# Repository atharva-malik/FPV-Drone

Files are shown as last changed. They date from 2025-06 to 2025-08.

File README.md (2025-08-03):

# Ghast Drone
While playing Minecraft, I entered the Ghast while in spectator mode, and wondered what it would be like to fly in it IRL. Therefore I designed the following project.
<p align="center">
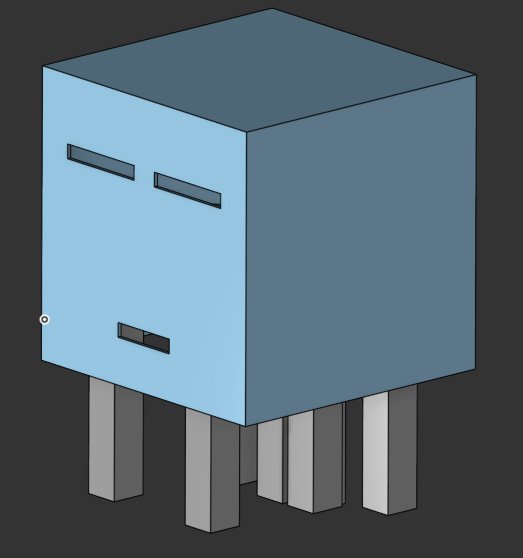
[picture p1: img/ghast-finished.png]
  
</p>
I have attached the picture of the look that I am going for. I will replace this with the finished build once it is done.

# BOM
The BOM is available in the [BOM.csv](BOM.csv) file. It contains all the parts required to build the drone, along with links to where they can be purchased. On a glance:
| Part Name | Source | Price |
|---|---|---|
|HappyModel EP1 EP2 RX 2.4G ExpressLRS| https://www.aliexpress.com/item/1005008247370304.html | $21.35|
|Custom Frame| \3D Models\Frame Base.stl | $30|
|iFlight XING-E Pro 2207 1800KV| https://www.aliexpress.com/item/1005007751252503.html | $85.66|
|Gemfan Hurricane 51477 3-Blade| https://www.aliexpress.com/item/1005008235140623.html | $4.29|
|SpeedyBee F405 Stack| https://www.aliexpress.com/item/1005005646570050.html | $136.07|
|Caddx Ratel 2 V2| https://www.aliexpress.com/item/1005006156850612.html | $30.67|
|XILO STAX 5.8GHz FPV Video Transmitter (25-600mW) w/ Smart Audio| https://www.getfpv.com/xilo-stax-5-8ghz-fpv-video-transmitter-25-600mw.html | $38.99|
|6S 1480mAh 150C Battery| https://www.aliexpress.com/item/1005007537503660.html | $73.84|
|Lipo Charger| https://uk.banggood.com/IMAX-B6-80W-6A-Lipo-Battery-Balance-Charger-T-Plug-with-Power-Supply-Adapter-p-1401686.html | $39.75|
|Heat Shrink| https://www.aliexpress.com/item/1005005088669576.html | $11.51|
|DVR| https://au.banggood.com/Eachine-ProDVR-Pro-DVR-Video-Audio-Mini-Recorder-for-FPV-Multicopters-for-RC-Drone-FPV-Racing-p-1061196.html | $16.11|
|GRAND TOTAL (AUD) | | $488.24|
|GRAND TOTAL (USD) | | $316.58|

The total cost currently comes out to ~$300 USD, bear in mind that this is without the cost of the 3D printed parts or the shipping costs. The cost of the drone parts will vary depending on where you live and where you buy the parts from.

# Firmware
For the firmware, I will be using the tried and tested [BetaFlight](https://betaflight.com/) firmware. This firmware is widely used in the FPV community and has a lot of features that will be useful for my drone. I should be able to customise it to give it the "floaty" feel of the Ghast.

# Wiring Instructions
All of the parts need to be wired according to the following schematic:
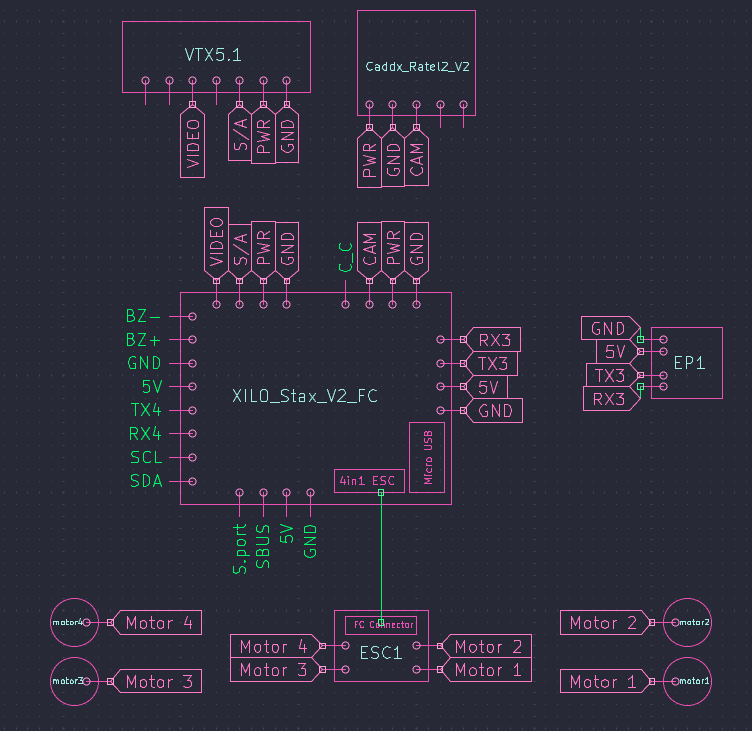
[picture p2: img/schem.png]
Schematic


# 3D Printed Parts
The 3D printed parts are all under the 3D Models folder in the repository. It contains the STL files for a carrying case, a GoPro mount, and the Ghast body and tentacles. The 3D printed parts are all designed to be printed with standard PLA filament.

# 3D Model
Drone

The 3D model of the Ghast is available in the [3D Models](/3D%20Models/Proof%20of%20Concept/).

# Frame Design
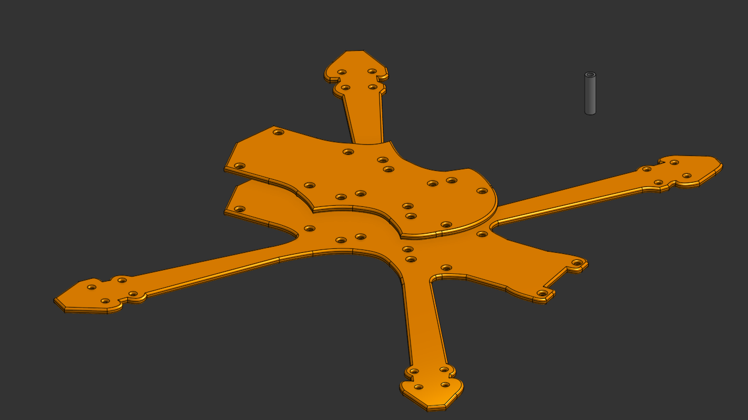
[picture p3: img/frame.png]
Frame


# Credits
I would like to thank @Mikuel for [this](https://www.aos-rc.com/aos-labs) link which explained drone motors to me.

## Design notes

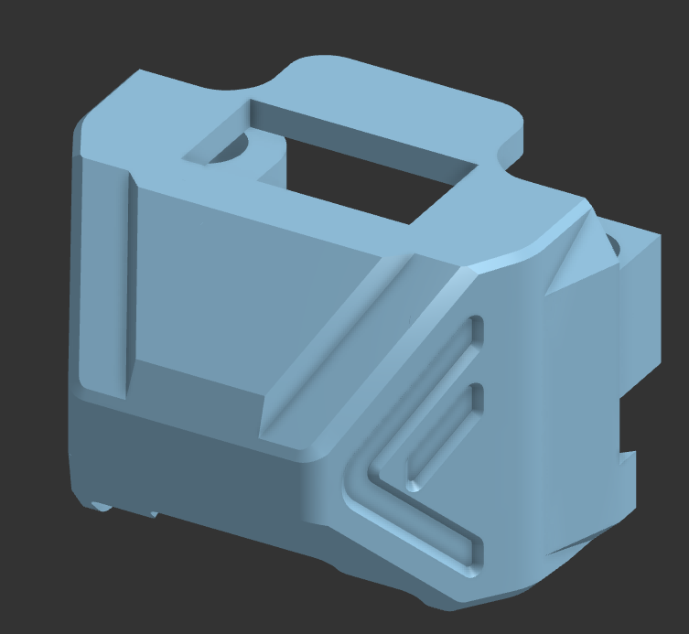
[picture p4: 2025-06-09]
img/POC/Backplate (XT60 Connector).png

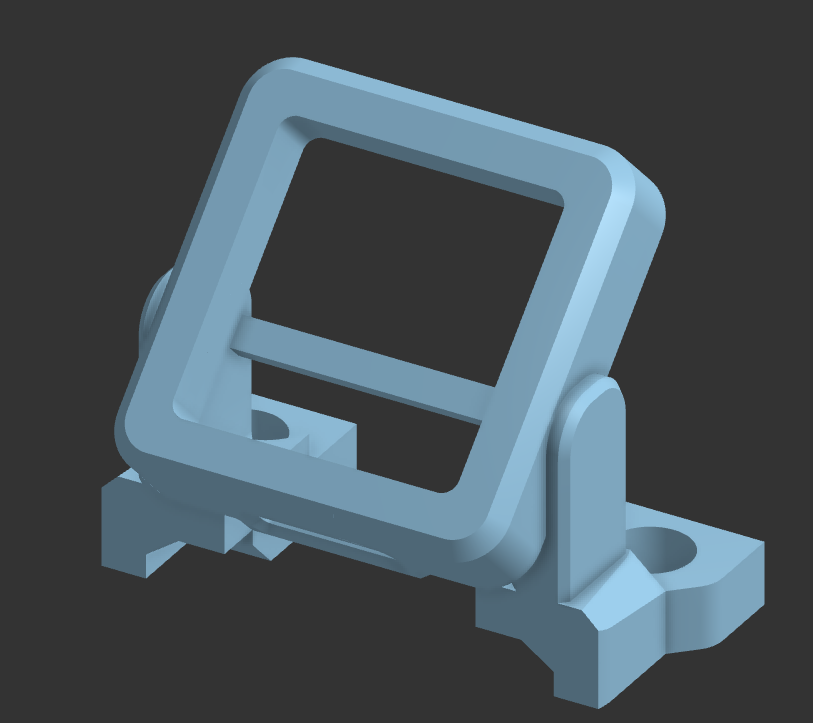
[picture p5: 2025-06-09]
img/POC/GPS Mount High.png

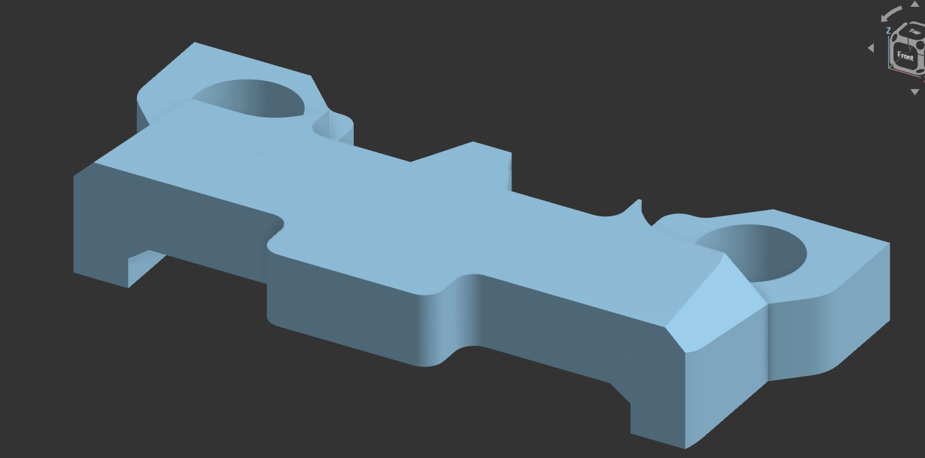
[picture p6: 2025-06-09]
img/POC/GPS - Flat Mount.png

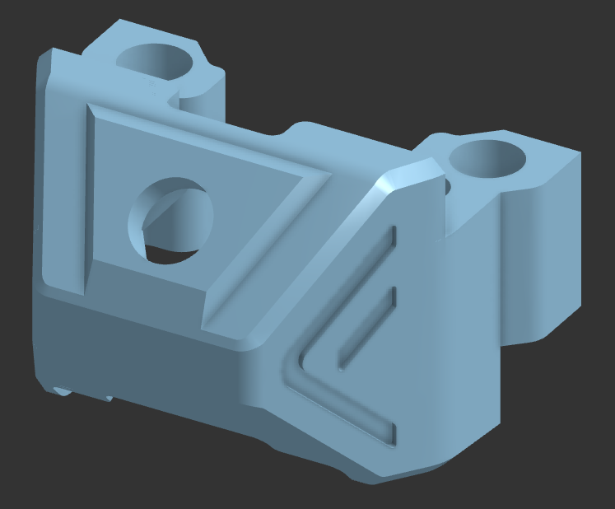
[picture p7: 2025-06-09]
img/POC/Analog Transmitter Mount.png

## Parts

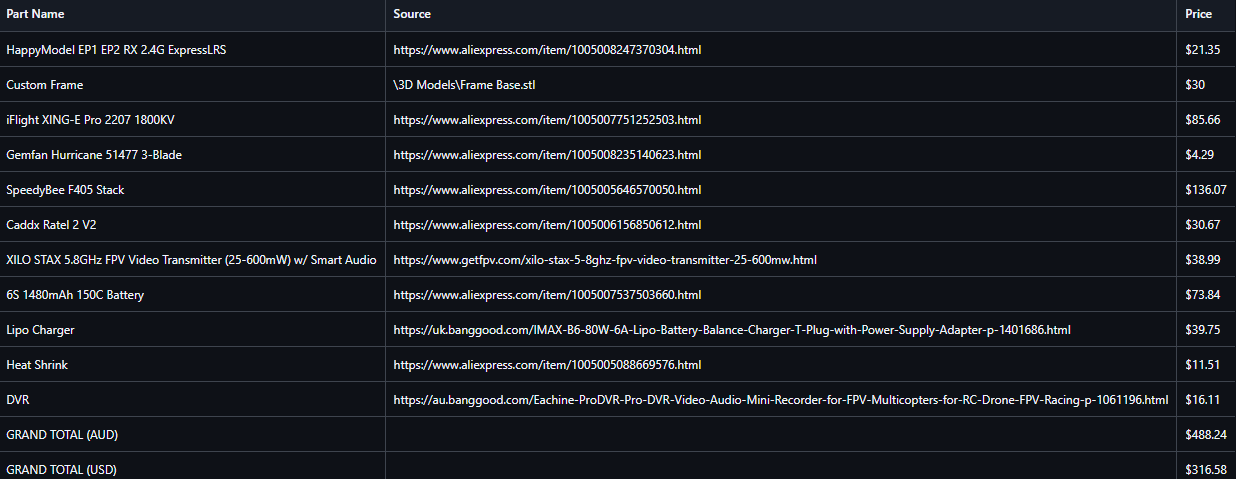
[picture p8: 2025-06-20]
img/BOM.png

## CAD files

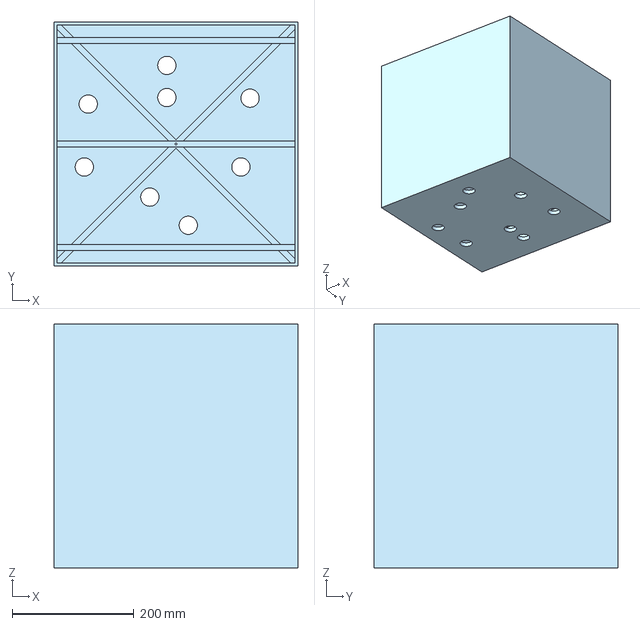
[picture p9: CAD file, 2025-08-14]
3D Models/Ghast Body.step
400.0 x 400.0 x 400.0 mm

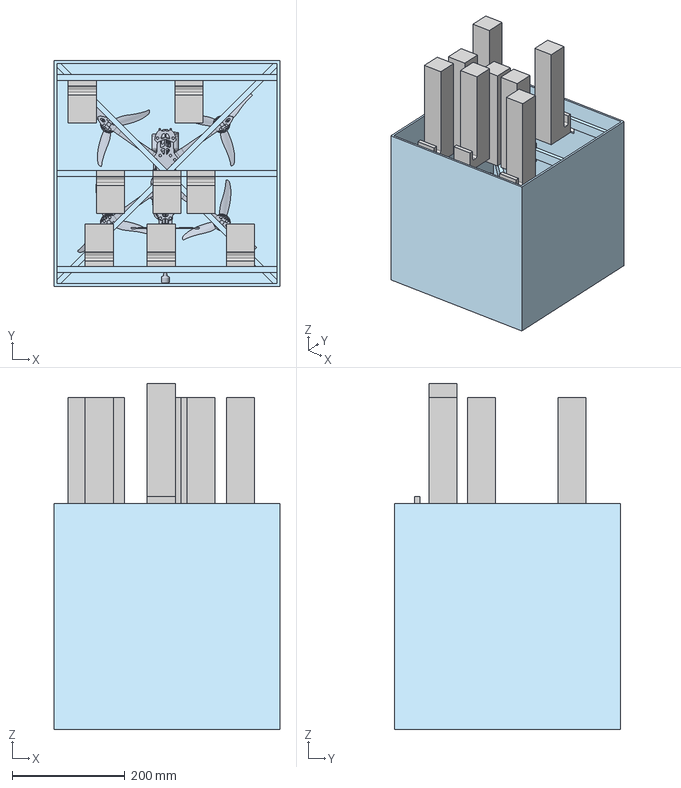
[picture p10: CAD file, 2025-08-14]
3D Models/Proof of Concept/Ghast - Clean.step
400.0 x 400.0 x 612.5 mm
Tentacle x 8
Ghast Body
id24
id29
id34
id39
id44
id49
id54
id59
id64
id69
id74
id79
id84
id89
id94
id99
id104
id109
id114
id119
id124
id129
id134
id139
id144
id149
id154
id159
id164
id169
id174
id179
id184
id189
id194
id199
id204
id209
id214
id219
id224
id229
id234
id239
id244
id249
id254
id259
id264
id269
id274
id279
id284
id289
id294
id299
id304
id309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

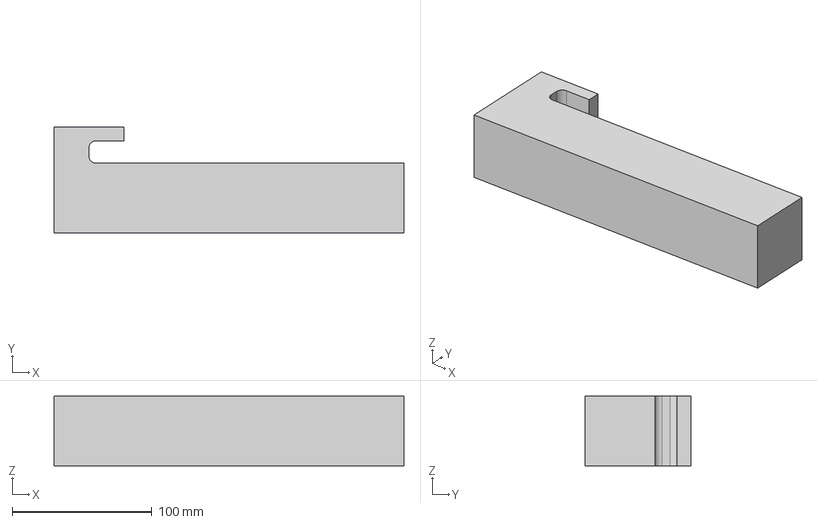
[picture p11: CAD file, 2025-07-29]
3D Models/Tentacle.step
250.0 x 76.0 x 50.0 mm

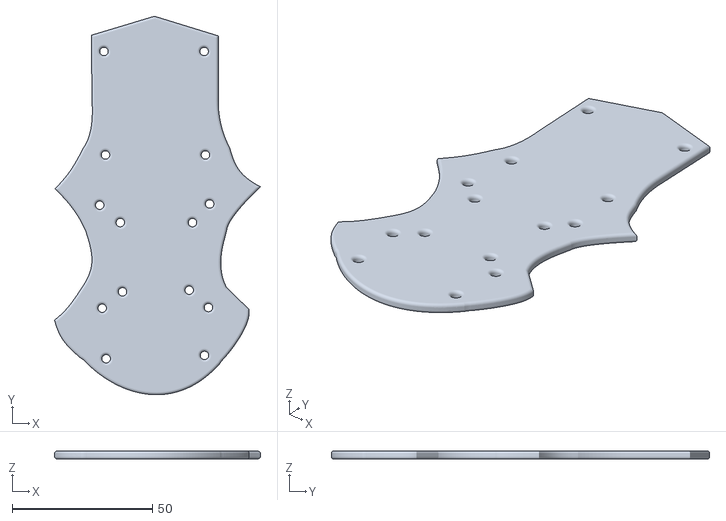
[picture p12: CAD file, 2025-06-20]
3D Models/Frame Top.stl
73.5 x 135.0 x 3.00

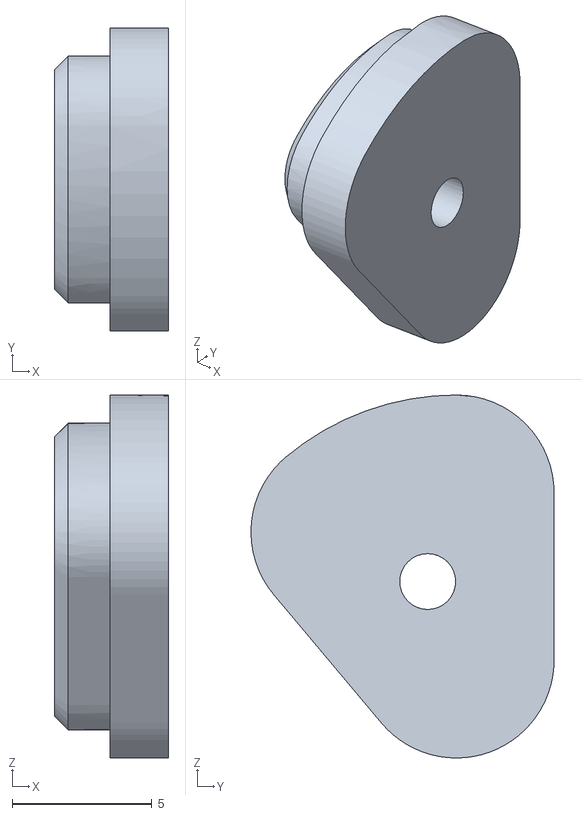
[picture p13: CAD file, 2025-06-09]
3D Models/Proof of Concept/Camera Mount (Analog).stl
4.10 x 10.9 x 13.0

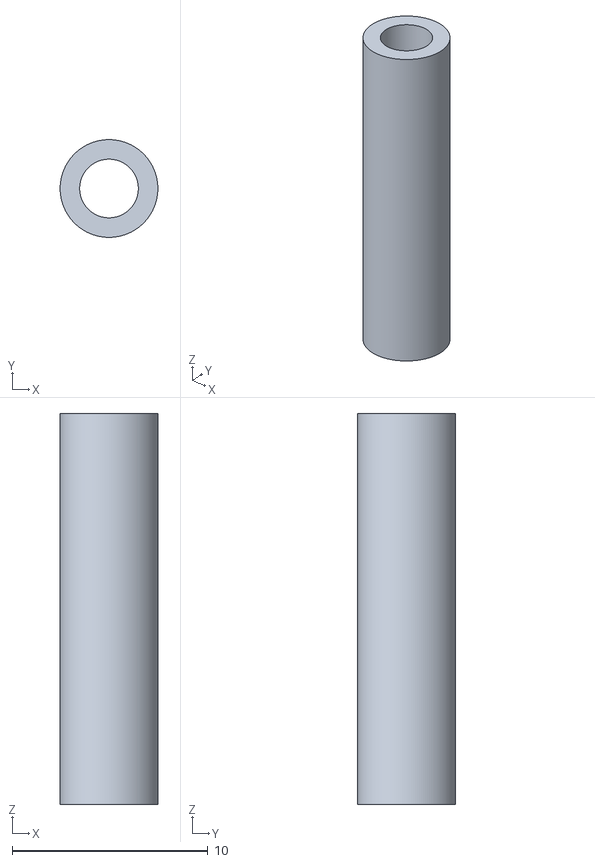
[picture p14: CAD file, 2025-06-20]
3D Models/Standoff.stl
5.00 x 5.00 x 20.0

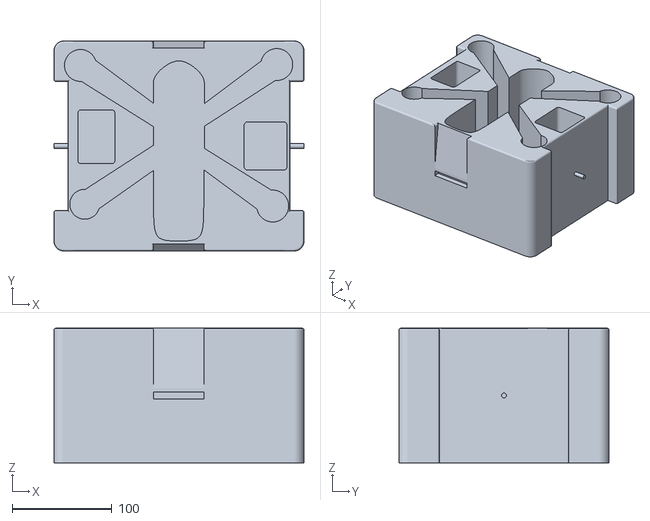
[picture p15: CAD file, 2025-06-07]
3D Models/Case Bottom.stl
250.8 x 210.8 x 135.0

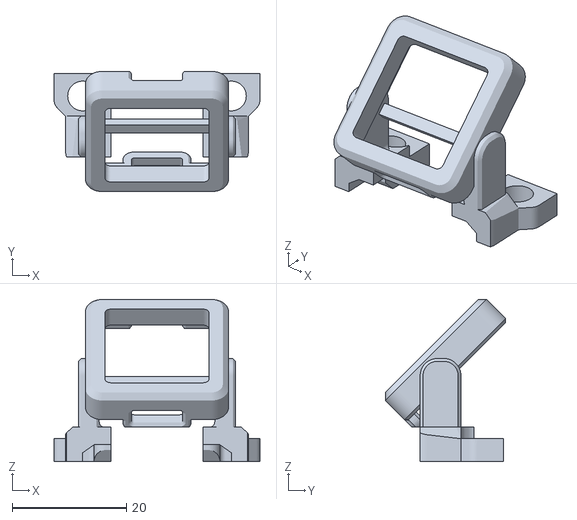
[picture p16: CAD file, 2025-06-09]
3D Models/Proof of Concept/GPS Mount High.stl
36.0 x 21.0 x 28.3

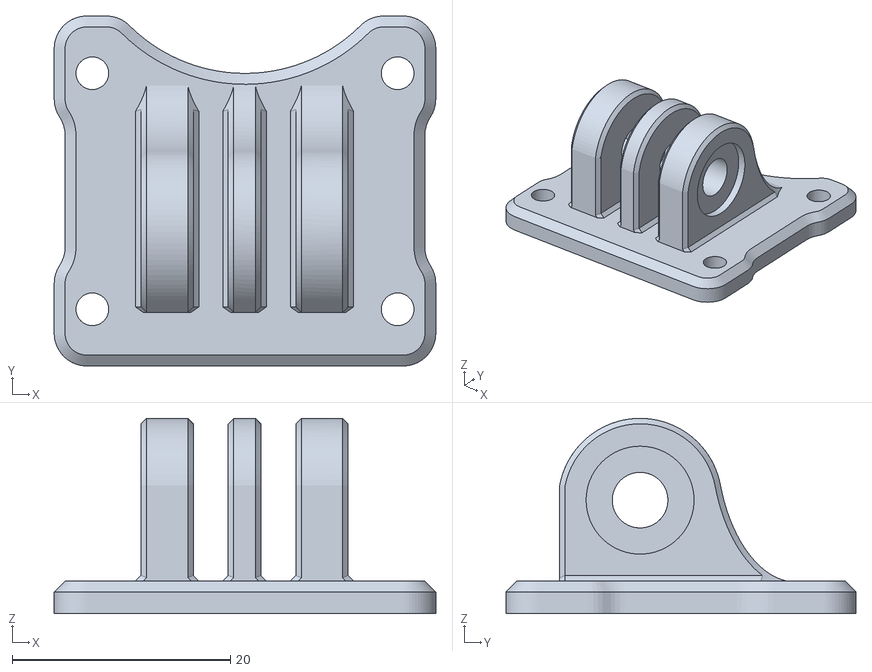
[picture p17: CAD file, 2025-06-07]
3D Models/GoPro Mount.stl
35.0 x 32.1 x 17.9

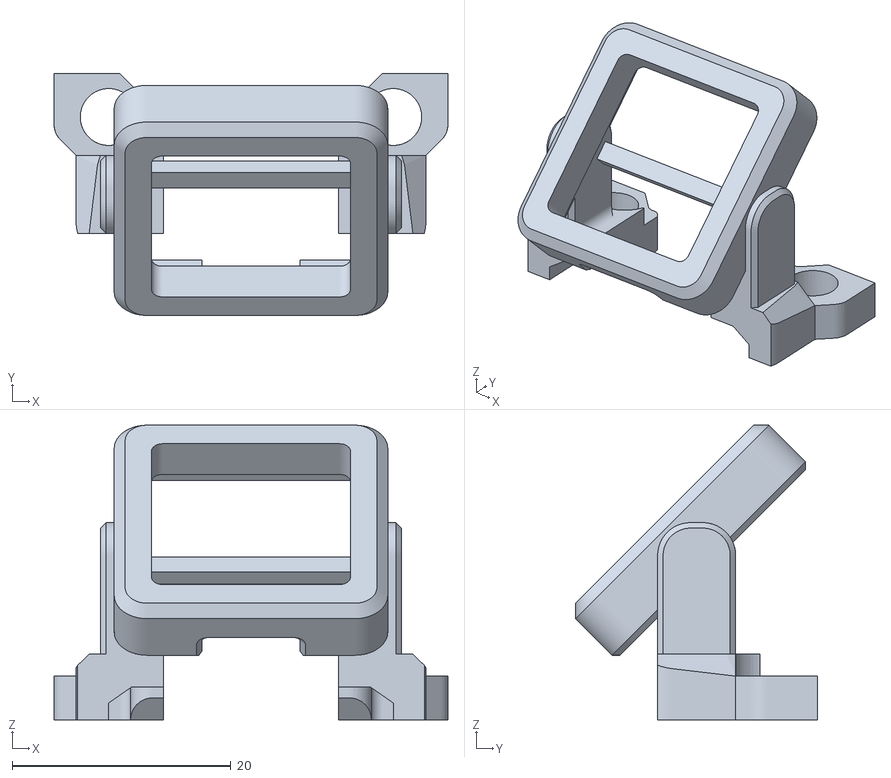
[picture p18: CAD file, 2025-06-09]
3D Models/Proof of Concept/M10 - GPS Mount.stl
36.0 x 22.1 x 26.9

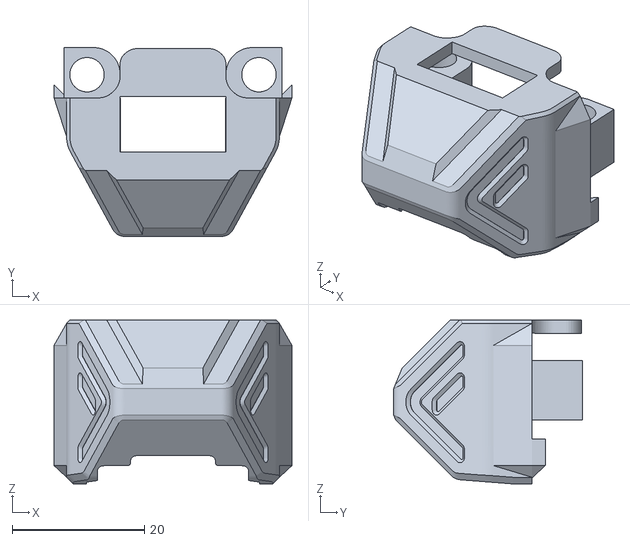
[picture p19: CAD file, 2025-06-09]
3D Models/Proof of Concept/Backplate (XT60 Connector).stl
36.0 x 28.5 x 24.8

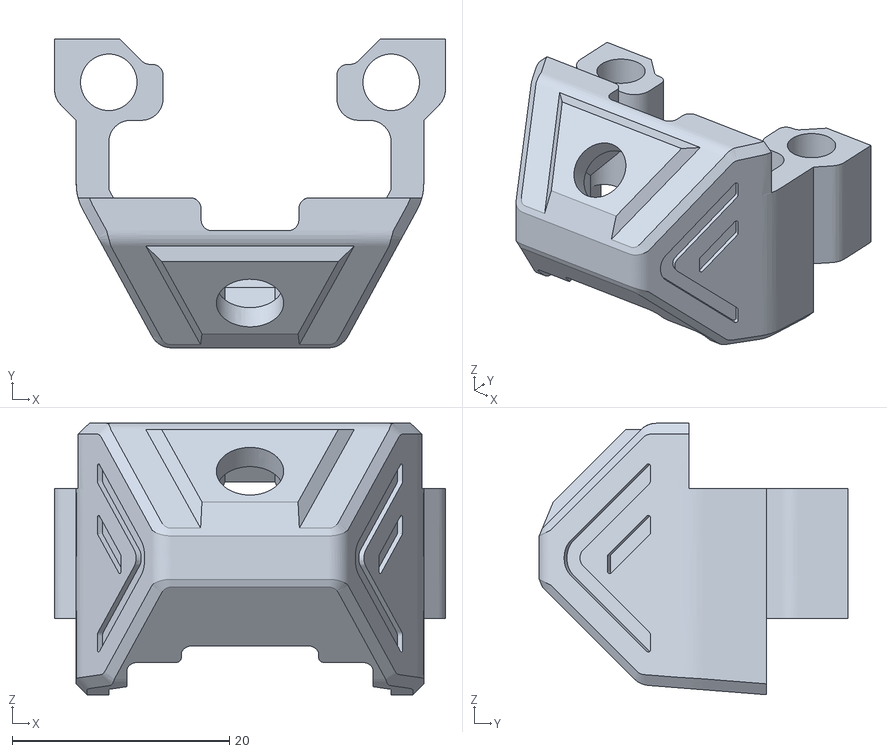
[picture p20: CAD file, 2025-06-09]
3D Models/Proof of Concept/Analog Transmitter Mount.stl
36.0 x 28.4 x 25.0

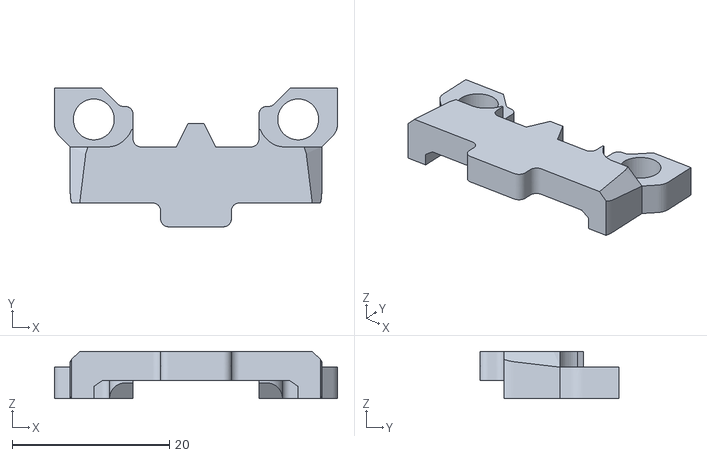
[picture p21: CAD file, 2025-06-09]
3D Models/Proof of Concept/GPS - Flat Mount.stl
36.0 x 17.6 x 6.00

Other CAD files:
3D Models/Proof of Concept/Ghast - With Airflow.step
3D Models/Proof of Concept/Ghast.stl
3D Models/Ghast Body.stl
3D Models/Tentacle.stl

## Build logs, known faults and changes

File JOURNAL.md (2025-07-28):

---
title: "Ghast drone"
author: "@Chaos"
description: "A drone that is flown as a Ghast"
created_at: "2025-05-06"
---
## Total Time Spent: 35 hrs
# May 5th: Researched Parts and started BOM

I am researching the parts required to build the drone. [This](https://oscarliang.com/) website has been a great help and has helped me finalise my parts list. The BOM will soon be added as a seperate file.


**Total time spent: 3h**

# May 6th: Made a Wiring Diagram

Now that I have the parts list, I started researching the datasheets of the individual parts. Luckily, most of the parts had a wiring diagram attached to the listing. Using these diagrams, I recreated them in KiCad and made up a schematic, with custom symbols for each part, for the drone. This should make it easier to wire the drone up later on.

schematic

You might notice that there are some unused pins. This is because I fully copied over the wiring diagrams from the parts, and some of them had more pins than I needed. I will leave them there in case someone wants to use the same parts but with different wiring and needs the symbols.

I was also looking at alternative parts, and one caught my eye: the [SPEEDYBEE F405 V3 Stack](https://www.fpvfaster.com.au/products/speedybee-f405-v3-flight-controller-bls-50a-esc-stack-30-5x30-5mm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). 
speedybee

It has a lot of similar features to the XILO Stax V2 I was planning to use, so I will be looking into it more. It is also cheaper, so I might end up using it instead. Tomorrow, I will try to finish the 3D model of the drone case and submit the project as the other 3D prints require precise measurements.

**Total time spent: 4h**

# May 7th: Started 3D Model
To start with, I did a lot more research on the parts, and ended up with a configuration that makes the most use of the budget, without over-spending on any one part. Through this, I was able to reduce the cost of the drone by ~$71 AUD.

Moving on, I started the 3D models. Since I am using a new frame, I had to spend way too much time looking for dimensions. Finally however, I found the dimensions of the frame and started modelling it in [OnShape](https://www.onshape.com/). While I am decent with CAD, I am not the best, so I decided to *not* model the frame itself, but rather just the case that will hold all the parts. The criteria I had for this case were:
- It should be able to hold all the parts required to film securely
- It should be compact
- It should be easy to print
- It should be aesthetically pleasing
- All parts must sit flush (OCD)
- It should *click* together, so no screws are required

With that decided, I finalised what I wanted to be able to fit in the case:
- GoPro Hero 13
- 6S LiPo pack
- 5" props (2 spaces, one for CW and one for ACW)
- Drone (duh)

The first step was to sketch out the bottom in 2D, and I ended up with this, using the image on the left as a reference:
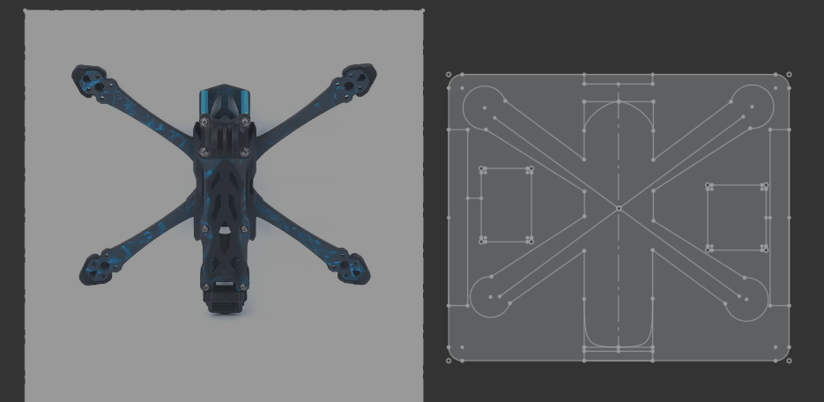
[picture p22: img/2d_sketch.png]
2D Sketch

Here, the two skinny rectangles on either side are the prop mounts (it will be more clear in the finished model), the rectangle to the left is the GoPro mount, and the rectangle on the right is the 6S LiPo pack mount. The rest is the drone itself, which will be mounted in the middle. As is apparent, I tried to keep everything tight, and therefore had to think outside the box (literally) to fit everything in. 

The next challenge to tackle was the click. Since I am not using screws, I had to make sure that the case would hold everything securely. To do this, I decided to use a click mechanism, where the top and bottom of the case would click together. This is done by having a lip on the top and a groove on the bottom, which will hold everything in place. To start with, I had this:
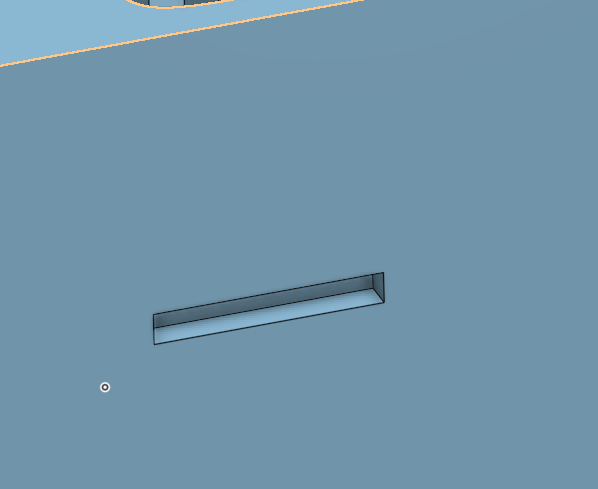
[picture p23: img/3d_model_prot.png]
Prototype 1


However, I quickly realised that this would not work, as the filament would not bend enough for the groove to hold the lip securely. So, I redesigned it to slope, which would allow the filament to bend more easily. This is what I ended up with, with a slope leading to the groove:

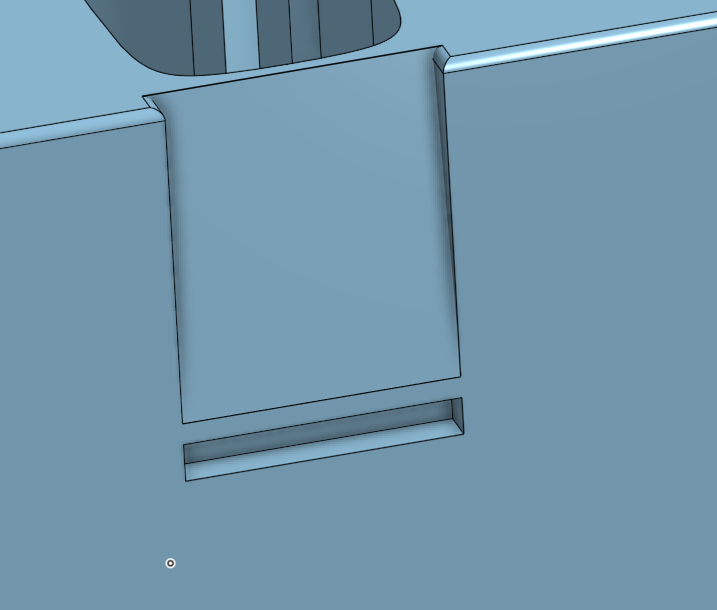
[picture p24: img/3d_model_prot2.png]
Prototype 2


I finished the bottom part of the case with filets to make it look nicer. I did *not* filet the bottom as it will lead to a harder print and won't have enough of an aesthetic impact to justify the harder and more complicated print. The final model of the bottom part looks like this:
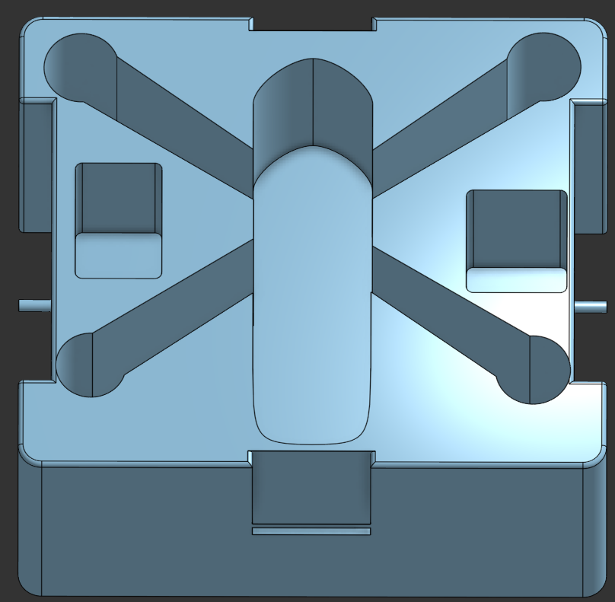
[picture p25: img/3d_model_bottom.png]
Bottom Part


As you can see, the sides are exposed. This is where the props will fit. You will be able to slip in two 5 inch props on either side. This, along with the top of the case clicking into the bottom, should hold everything securely in place.

Moving on to the top part, I wanted something simple and professional to match the aesthetic so far. Therefore, I ended up going with a simple box design, with the lip on the inside to latch onto the groove on the bottom. I'll let the design speak for itself:
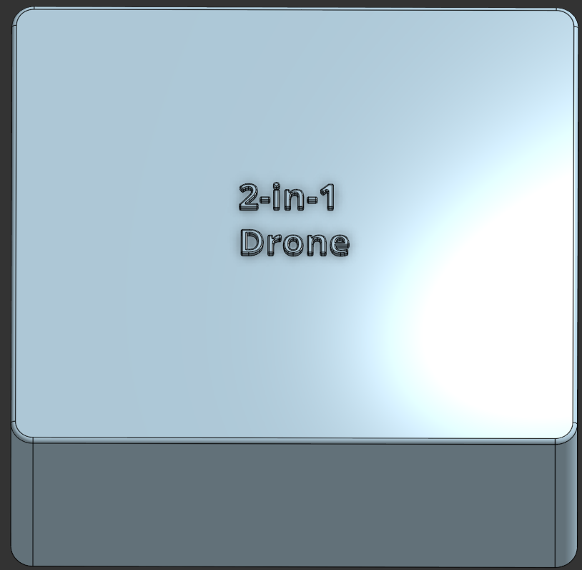
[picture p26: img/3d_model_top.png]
Top Part


I added filets to the text at the top as well, to match the round-ish aesthetic of the bottom part. Overall I am very happy with the design so far, and I think it will work well. The next step was to model the motor guards and the GoPro mount. That was not that hard, and I will not bore you with the details. All of these models are attached to the 3D Models folder in the repository.

**Total time spent: 6h**

## May 8th: Resubmitting with more Images
As @Cyao pointed out, I did not have enough images in my repo, so I will be adding more images to the repo along with more thorough explanations of design choices of the carrying case.

### 1. Case Design Explanation
Something that might be better explained with the following image (excusing my horrible drawing skills):
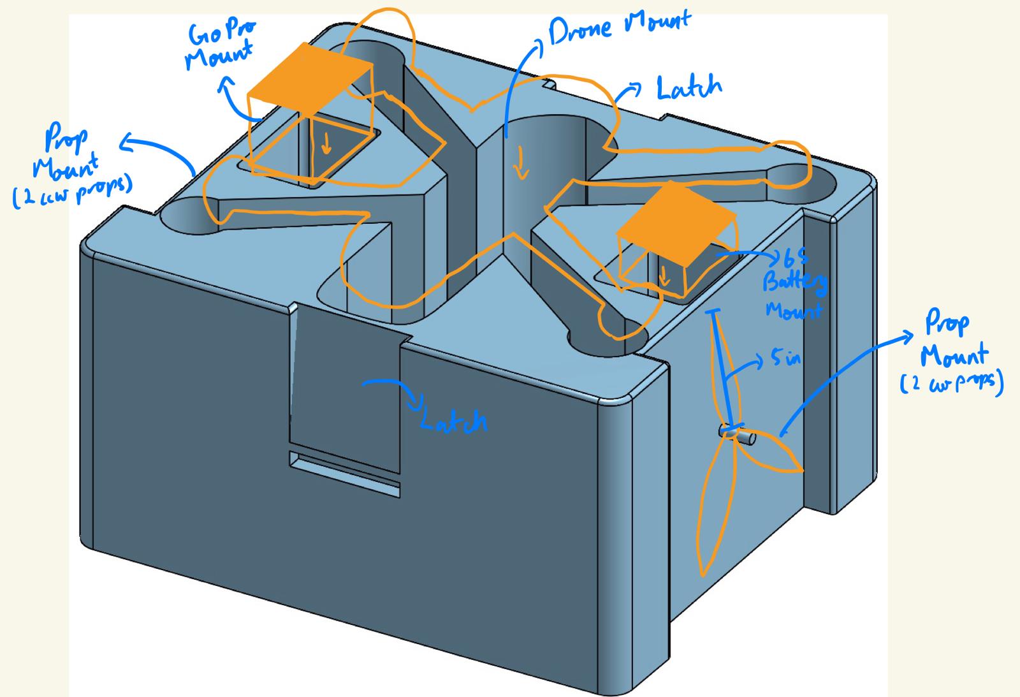
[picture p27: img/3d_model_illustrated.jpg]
Illustrated Model

The case is designed to hold *everything* you would take on a field trip. The hardest part to cater for was the Props, as they are quite long and would not fit in a normal case. Therefore, I had to design the case to hold them on the sides, which is why the case is so tall. They are 5 inch props (5 in diameter), so I decided to make a similar mount as to the motor, which is why there is a protrusion on the side. Rest everything should fit in as illustrated in the image above.

### 2. Latch Mechanism Explanation
The satisfying click that I was craving was achieved by having a lip on the top part of the case and a groove on the bottom part. As mentioned above, I started with a flat cross-section, as shown in Fig. 1:
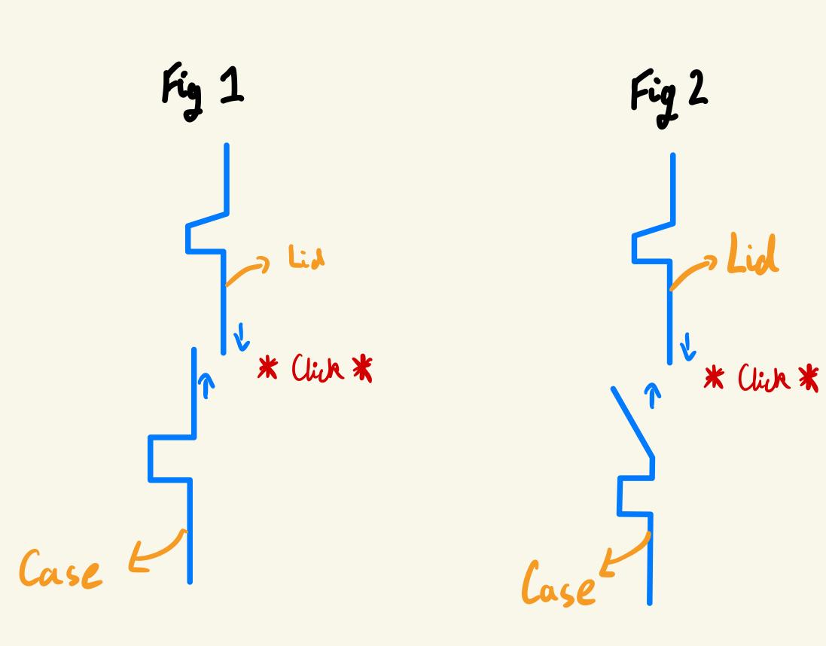
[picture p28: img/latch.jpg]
Latch Diagrams

However, I quickly realised that this would not work, as the filament would not bend enough for the lip to be able to slide down into the groove. Therefore, I redesigned it to have a slope, which would allow the filament to bend more easily. This is shown in Fig. 2

**Total time spent: 2h**

# May 9th: Made more 3D Models
At @Cyao's suggestion, I made more 3D models of the drone. These are proof of concept models, and are not the final models. They are designed to show how the drone will look like when it is finished. The dimensions will be perfected once I have the parts at hand, but for now, these models should give a good idea of how the drone will look like. All pics for them can be found in the [img folder](img/poc/).

**Total time spent: 3h**

# May 10th: Modelled and Sculpted the Drone
Since @Cyao was insistent on having a 3D model of the drone, I decided to model it in Blender. It was a long process, but I am happy with the result. I chose Blender over OnShape as I am more comfortable with it, and thought it will allow better looking model. This is the result.
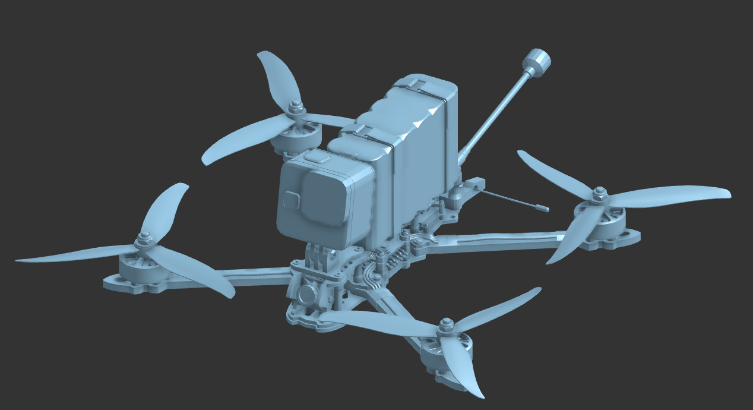
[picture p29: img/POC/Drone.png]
Drone

Also, side note, I imported it into OnShape as I like the default texturing better than Blender's static grey.

I also added all of these images in README.md, so you can see them there as well.

**Total time spent: 7h**

# May 17th-20th: Modelled the Drone Frame and Standoffs
After spending considerable time researching ([best resource](https://github.com/ps915/source_two)) and looking through drone frames, I started making my own. I did not want to change the things I had already modelled, so using those, along with the parts list as reference, I ended up with the frame pictured below.
Frame+Standoff
The main problem, along with taking care of all of the measurements, was to address aerodynamics to some degree. The main problem is that you don't want sharp edges, because although it may seem more intuitive, at sub-sonic speeds, it just ends up increasing drag and disrupting airflow. So, I tried to counteract that by fillet-ing the front and sides of the drone. This should help 'guide' the air around the frame, reducing friction. Along with that, I made the standoffs be the drone standard of 20 mm high, with M3 holes.
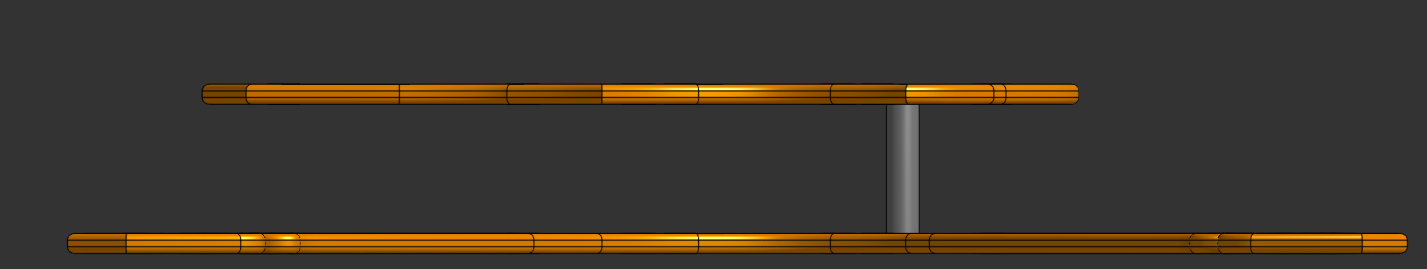
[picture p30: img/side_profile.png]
Side profile

Overall, while it may not look like much, I am proud of this design and am surprised by how much thought needs to be put in when designing and considering the placements of parts.

**Total time spent: 7h**

# July 28th: Project Redesign

I had honestly given up on this project as you may be able to tell from the huge gap in the journal. During this time I was mainly focused on my upcoming assessments and this project took the back seat. However, while playing around in Minecraft, I was flying as a Ghast and therefore was wondering how enjoyable it would be to fly like that irl.

While doing that, this project came to mind and I revisited it. I had already almost finished the frame. So I implemented the feedback I had received on it from the highway channel. 

After finishing the frame, I started designing the Ghast, using the following images as a reference:
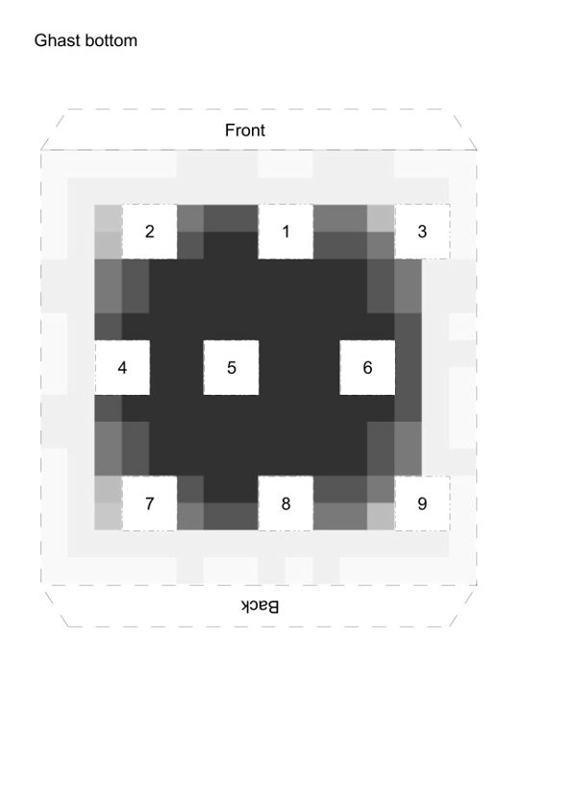
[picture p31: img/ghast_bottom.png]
Ghast bottom

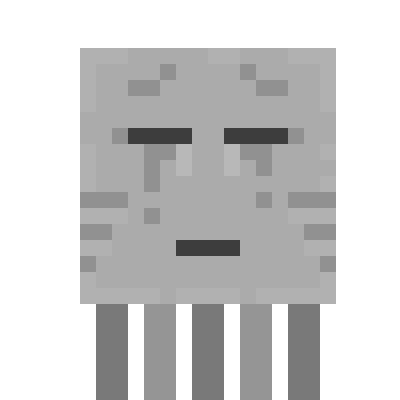
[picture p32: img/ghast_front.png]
Ghast front


These images combined with the fact that I knew the Ghast was 4x4x4 blocks, allowed me to fully model it. Note that I decided to go for 8 tentacles instead of the 9 as that seems to be the most common amount.

For the tentacles, I wanted something more than just stationary, fixed rectangles, so I added three gantries to the bottom of the Ghast's body along with fillet's on the tentacles so that they can be re-ordered, added and removed as per the user's decision. The fillets will also allow them to interact with the air around, giving it a more realistic look. 

I decided to fit the camera on the left eye and ensured to leave enough of a gap that it would fit.

The rest of the BOM remains unchanged as the Ghast will be printed thanks to the printer legion

**Total time spent: 5h**

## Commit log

2025-06-06 Update BOM.csv
    Fixed totals
    [BOM.csv]
2025-06-06 updated journal
    added today's entry and fixed yesterday's date
    [Wiring Schematics.kicad_pcb, Wiring Schematics.kicad_sch]
2025-06-07 journal and bom update
    [BOM.csv, Case Bottom.stl, GoPro Mount.stl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]
2025-06-09 Added more models
    [Analog Transmitter Mount.stl, Backplate (XT60 Connector).stl, Camera Mount (Analog).stl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]
2025-07-29 Added .STEPs
    [Ghast Body.step, Tentacle.step]
2025-08-14 Update Ghast Body.step
    [Ghast Body.step]
